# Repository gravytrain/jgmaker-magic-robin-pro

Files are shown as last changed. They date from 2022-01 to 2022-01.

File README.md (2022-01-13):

# Firmware For JGMaker Magic with MKS Robin Pro Board

## Official JGMaker ArtistD Firmware 
* Get the latest release of the Official Firmware: https://github.com/JGMaker3dofficial/artistd/releases/latest
## Official JGMaker Magic Firmware 
* Get the Official Firmware: https://github.com/JGMaker3dofficial/magic
## MKS Robin Pro Pinouts
[MKS Robin Pro Pinout](https://github.com/makerbase-mks/MKS-Robin-Pro/blob/master/hardware/MKS%20Robin%20Pro%20V1.0_001/MKS%20Robin%20Pro%20V1.0_001%20PIN.pdf)

## Setting up the new board

1.  Label all the wires as you remove them from the hotend connector.
2.  Fan connections only have a negative wire.
3.  The X-Endstop Ground wire is shared with the TH1- wire. If you reverse the TH1 - and + wires you will throw a thermal error when you trigger the X-Endstop connection.  Fix by reversing the TH1 wires.
### Mounting the board

1. Included in this project is a very basic mount 'MKS_Robin_Pro_Mount.stl'.  The board is mounted offset from the original alignment because the USB and Card slots cant align with this board.  There is enough offset to connect a usb cable and be able to slide the SD Card in and out of the slot.
2. Attach the board to the mount using (4) M3x8mm Screws with M3 nuts on the back.
3. Use 3 old board screws to secure the mount to the frame. The 4th hole under the new board will remain unattached, but doesnt affect the secureness of the mount.
### Hotend Pinout
                      Connector Clip Orientation -->
                      +--------+
                 X-S  |1*     6|  TH1+ (PC1)
      TH1-/X-G (PC1)  |2      7|  J1- (12/24v)
         HE0+ (PF10)  |3      8|  PB1- (FAN)
         HE0+ (PF10)  |4      9|  HE0- (PF10)
         HE0+ (PF10)  |5     10|  HE0- (PF10)
                      +--------+
             
### Bed Pinout

1. Connect both Red Wires together into PA0-.
2. Connect both Black Wires together into PA0+.
3. Connect the two remaining White wires to TB(PC0) for Bed Thermistor ( you will need to extend the length of these two wires so that the bed can freely move back and forth without pulling these wires tight).

### UART Board Jumpers

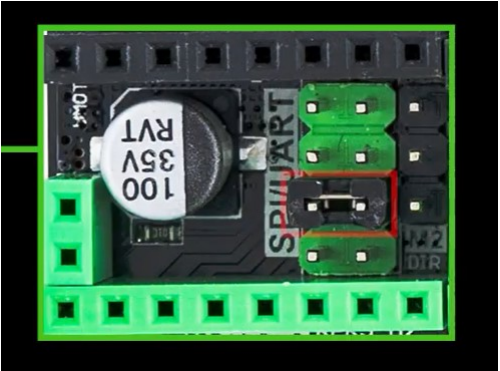
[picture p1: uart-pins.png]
Uart Board Jumpers


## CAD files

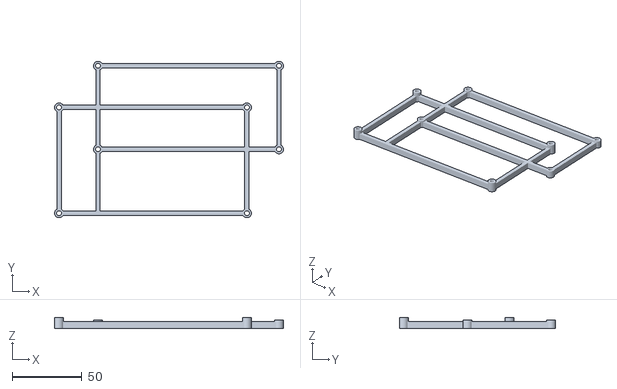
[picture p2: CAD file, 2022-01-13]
MKS_Robin_Pro_Mount.stl
164.5 x 112.4 x 8.00

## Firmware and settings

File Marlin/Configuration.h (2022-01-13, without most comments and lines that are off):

#pragma once
#define CONFIGURATION_H_VERSION 020007
#define STRING_CONFIG_H_AUTHOR "DryGravyTrain" // Who made the changes.
#define CUSTOM_VERSION_FILE Version.h // Path from the root directory (no quotes)
#define SHOW_BOOTSCREEN
#define SHOW_CUSTOM_BOOTSCREEN
#define SERIAL_PORT -1
#define SERIAL_PORT_2 3
#define BAUDRATE 115200
  #define MOTHERBOARD BOARD_MKS_ROBIN_PRO
#define CUSTOM_MACHINE_NAME "Elsie & Zeke's Maker"
#define EXTRUDERS 1
#define DEFAULT_NOMINAL_FILAMENT_DIA 1.75
#define HOTEND_OFFSET_Y { 0.0, 0.5 }  //{ 0.0, 1.00 }  // (mm) relative Y-offset for each nozzle  Y轴相对喷头的偏移量    第一台为 0.2  增加向前，减小向后  CTM关闭
#define HOTEND_OFFSET_Z { 0.0, 0.1 }  // (mm) relative Z-offset for each nozzle
#define TEMP_SENSOR_0 1
#define TEMP_SENSOR_1 0
#define TEMP_SENSOR_2 0
#define TEMP_SENSOR_3 0
#define TEMP_SENSOR_4 0
#define TEMP_SENSOR_5 0
#define TEMP_SENSOR_6 0
#define TEMP_SENSOR_7 0
#define TEMP_SENSOR_BED 1  //JGMaker
#define TEMP_SENSOR_PROBE 0
#define TEMP_SENSOR_CHAMBER 0
#define DUMMY_THERMISTOR_998_VALUE 25
#define DUMMY_THERMISTOR_999_VALUE 100
#define MAX_REDUNDANT_TEMP_SENSOR_DIFF 10
#define TEMP_RESIDENCY_TIME     10  // (seconds) Time to wait for hotend to "settle" in M109
#define TEMP_WINDOW              1  // (°C) Temperature proximity for the "temperature reached" timer
#define TEMP_HYSTERESIS          3  // (°C) Temperature proximity considered "close enough" to the target
#define TEMP_BED_RESIDENCY_TIME 10  // (seconds) Time to wait for bed to "settle" in M190
#define TEMP_BED_WINDOW          1  // (°C) Temperature proximity for the "temperature reached" timer
#define TEMP_BED_HYSTERESIS      3  // (°C) Temperature proximity considered "close enough" to the target
#define HEATER_0_MINTEMP   5
#define HEATER_1_MINTEMP   0
#define HEATER_2_MINTEMP   0
#define HEATER_3_MINTEMP   0
#define HEATER_4_MINTEMP   0
#define HEATER_5_MINTEMP   0
#define HEATER_6_MINTEMP   0
#define HEATER_7_MINTEMP   0
#define BED_MINTEMP        5
#define HEATER_0_MAXTEMP 275
#define HEATER_1_MAXTEMP 275
#define HEATER_2_MAXTEMP 275
#define HEATER_3_MAXTEMP 275
#define HEATER_4_MAXTEMP 275
#define HEATER_5_MAXTEMP 275
#define HEATER_6_MAXTEMP 275
#define HEATER_7_MAXTEMP 275
#define BED_MAXTEMP      130 //TwinkieXLII
#define PIDTEMP
#define BANG_MAX 255     // Limits current to nozzle while in bang-bang mode; 255=full current
#define PID_MAX BANG_MAX // Limits current to nozzle while PID is active (see PID_FUNCTIONAL_RANGE below); 255=full current
#define PID_K1 0.95      // Smoothing factor within any PID loop
  #define PID_AUTOTUNE_MENU     // Add PID auto-tuning to the "Advanced Settings" menu. (~250 bytes of PROGMEM)
    #define DEFAULT_Kp  22.20
    #define DEFAULT_Ki   1.08
    #define DEFAULT_Kd 114.00
#define MAX_BED_POWER 255 // limits duty cycle to bed; 255=full current
  #define PID_FUNCTIONAL_RANGE 10 // If the temperature difference between the target temperature and the actual temperature
#define PREVENT_COLD_EXTRUSION
#define EXTRUDE_MINTEMP 170
#define PREVENT_LENGTHY_EXTRUDE
#define EXTRUDE_MAXLENGTH 2000
#define THERMAL_PROTECTION_HOTENDS // Enable thermal protection for all extruders
#define THERMAL_PROTECTION_BED     // Enable thermal protection for the heated bed
#define USE_XMIN_PLUG
#define USE_YMIN_PLUG
#define USE_ZMIN_PLUG
#define ENDSTOPPULLUPS
#define X_MIN_ENDSTOP_INVERTING true  // Set to true to invert the logic of the endstop.
#define Y_MIN_ENDSTOP_INVERTING true  // Set to true to invert the logic of the endstop.
#define Z_MIN_ENDSTOP_INVERTING true  // Set to true to invert the logic of the endstop.
#define X_MAX_ENDSTOP_INVERTING true  // Set to true to invert the logic of the endstop.
#define Y_MAX_ENDSTOP_INVERTING true  // Set to true to invert the logic of the endstop.  //TwinkieXLII  已确认正确
#define Z_MAX_ENDSTOP_INVERTING true // Set to true to invert the logic of the endstop. //DryGravyTrain
#define Z_MIN_PROBE_ENDSTOP_INVERTING true // Set to true to invert the logic of the probe. //DryGravyTrain
#define X_DRIVER_TYPE TMC2209
#define Y_DRIVER_TYPE TMC2209
#define Z_DRIVER_TYPE TMC2209
#define E0_DRIVER_TYPE TMC2209
#define DISTINCT_E_FACTORS   //TwinkieXLII
#define DEFAULT_AXIS_STEPS_PER_UNIT   { 80, 80, 800, 88 } //DryGravyTrain
#define DEFAULT_MAX_FEEDRATE          { 300, 300, 5, 25 } //DryGravyTrain
#define DEFAULT_MAX_ACCELERATION      { 2000, 2000, 100, 10000 } //{ 500, 500, 100, 10000 }  TwinkieXLII
#define DEFAULT_ACCELERATION          500    // X, Y, Z and E acceleration for printing moves
#define DEFAULT_RETRACT_ACCELERATION  500    // E acceleration for retracts
#define DEFAULT_TRAVEL_ACCELERATION   500    // X, Y, Z acceleration for travel (non printing) moves
#define DEFAULT_EJERK    5.0  // May be used by Linear Advance
  #define JUNCTION_DEVIATION_MM 0.013 // (mm) Distance from real junction edge
  #define JD_HANDLE_SMALL_SEGMENTS    // Use curvature estimation instead of just the junction angle
#define S_CURVE_ACCELERATION
#define Z_MIN_PROBE_USES_Z_MIN_ENDSTOP_PIN
#define PROBE_MANUALLY
#define MANUAL_PROBE_START_Z 0.2 //TwinkieXLII
#define NOZZLE_TO_PROBE_OFFSET { 0, 0, 0 }
#define PROBING_MARGIN 10
#define XY_PROBE_SPEED (133*60)
#define Z_PROBE_SPEED_FAST HOMING_FEEDRATE_Z
#define Z_PROBE_SPEED_SLOW (Z_PROBE_SPEED_FAST / 2)
#define Z_CLEARANCE_DEPLOY_PROBE   10 // Z Clearance for Deploy/Stow
#define Z_CLEARANCE_BETWEEN_PROBES  5 // Z Clearance between probe points
#define Z_CLEARANCE_MULTI_PROBE     5 // Z Clearance between multiple probes
#define Z_PROBE_LOW_POINT          -2 // Farthest distance below the trigger-point to go before stopping
#define Z_PROBE_OFFSET_RANGE_MIN -20
#define Z_PROBE_OFFSET_RANGE_MAX 20
#define X_ENABLE_ON 0
#define Y_ENABLE_ON 0
#define Z_ENABLE_ON 0
#define E_ENABLE_ON 0 // For all extruders
#define DISABLE_X false
#define DISABLE_Y false
#define DISABLE_Z false
#define DISABLE_E false             // Disable the extruder when not stepping
#define DISABLE_INACTIVE_EXTRUDER true  // Keep only the active extruder enabled //DryGravyTrain
#define INVERT_X_DIR true   //DryGravyTrain
#define INVERT_Y_DIR false
#define INVERT_Z_DIR false
#define INVERT_E0_DIR false   //DryGravyTrain
#define INVERT_E1_DIR false
#define INVERT_E2_DIR false
#define INVERT_E3_DIR false
#define INVERT_E4_DIR false
#define INVERT_E5_DIR false
#define INVERT_E6_DIR false
#define INVERT_E7_DIR false
#define X_HOME_DIR -1
#define Y_HOME_DIR -1
#define Z_HOME_DIR -1
#define X_BED_SIZE 230
#define Y_BED_SIZE 230
#define X_MIN_POS -13 //DryGravyTrain
#define Y_MIN_POS -13
#define Z_MIN_POS 0
#define X_MAX_POS X_BED_SIZE
#define Y_MAX_POS Y_BED_SIZE
#define Z_MAX_POS 250
#define MIN_SOFTWARE_ENDSTOPS
  #define MIN_SOFTWARE_ENDSTOP_X
  #define MIN_SOFTWARE_ENDSTOP_Y
#define MAX_SOFTWARE_ENDSTOPS
  #define MAX_SOFTWARE_ENDSTOP_X
  #define MAX_SOFTWARE_ENDSTOP_Y
  #define MAX_SOFTWARE_ENDSTOP_Z
#define FILAMENT_RUNOUT_SENSOR
  #define NUM_RUNOUT_SENSORS   1     // Number of sensors, up to one per extruder. Define a FIL_RUNOUT#_PIN for each. //DryGravyTrain
  #define FIL_RUNOUT_STATE     HIGH  // Pin state indicating that filament is NOT present.
  #define FIL_RUNOUT_PULLUP          // Use internal pullup for filament runout pins.
  #define FILAMENT_RUNOUT_SCRIPT "M600"
  #define FILAMENT_RUNOUT_DISTANCE_MM 100  //TwinkieXLII
#define MESH_BED_LEVELING
#define RESTORE_LEVELING_AFTER_G28  //TwinkitXLII
#define DEBUG_LEVELING_FEATURE
  #define ENABLE_LEVELING_FADE_HEIGHT
  #define SEGMENT_LEVELED_MOVES
  #define LEVELED_SEGMENT_LENGTH 5.0 // (mm) Length of all segments (except the last one)
  #define G26_MESH_VALIDATION
    #define MESH_TEST_NOZZLE_SIZE    0.4  // (mm) Diameter of primary nozzle.
    #define MESH_TEST_LAYER_HEIGHT   0.2  // (mm) Default layer height for the G26 Mesh Validation Tool.
    #define MESH_TEST_HOTEND_TEMP  205    // (°C) Default nozzle temperature for the G26 Mesh Validation Tool.
    #define MESH_TEST_BED_TEMP      60    // (°C) Default bed temperature for the G26 Mesh Validation Tool.
    #define G26_XY_FEEDRATE         20    // (mm/s) Feedrate for XY Moves for the G26 Mesh Validation Tool.
    #define G26_RETRACT_MULTIPLIER   1.0  // G26 Q (retraction) used by default between mesh test elements.
  #define MESH_INSET 10          // Set Mesh bounds as an inset region of the bed
  #define GRID_MAX_POINTS_X 4    // Don't use more than 7 points per axis, implementation limited.
  #define GRID_MAX_POINTS_Y GRID_MAX_POINTS_X
#define LCD_BED_LEVELING  //TwinkieXLII
  #define MESH_EDIT_Z_STEP  0.025 // (mm) Step size while manually probing Z axis.
  #define LCD_PROBE_Z_RANGE 4     // (mm) Z Range centered on Z_MIN_POS for LCD Z adjustment
  #define MESH_EDIT_MENU        // Add a menu to edit mesh points
#define LEVEL_BED_CORNERS
  #define LEVEL_CORNERS_INSET_LFRB { 40, 40, 40, 40 } // (mm) Left, Front, Right, Back insets
  #define LEVEL_CORNERS_HEIGHT      0.0   // (mm) Z height of nozzle at leveling points
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

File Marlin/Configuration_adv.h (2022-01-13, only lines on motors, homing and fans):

#define E0_AUTO_FAN_PIN -1
#define E1_AUTO_FAN_PIN -1
#define E2_AUTO_FAN_PIN -1
#define E3_AUTO_FAN_PIN -1
#define E4_AUTO_FAN_PIN -1
#define E5_AUTO_FAN_PIN -1
#define E6_AUTO_FAN_PIN -1
#define E7_AUTO_FAN_PIN -1
#define CHAMBER_AUTO_FAN_PIN -1
#define HOMING_BUMP_MM      { 5, 5, 2 }       // (mm) Backoff from endstops after first bump
#define HOMING_BUMP_DIVISOR { 2, 2, 4 }       // Re-Bump Speed Divisor (Divides the Homing Feedrate)
#define QUICK_HOME                          // If G28 contains XY do a diagonal move first
#define HOME_AFTER_DEACTIVATE  // Require rehoming after steppers are deactivated
#define BACKLASH_COMPENSATION   //  TwinkieXLII
  #define BACKLASH_DISTANCE_MM { 0, 0, 0 } // (mm)
  #define BACKLASH_CORRECTION    1         // 0.0 = no correction; 1.0 = full correction
  #define BACKLASH_SMOOTHING_MM 3 // (mm)  TwinkieXLII
  #define BACKLASH_GCODE  //TwinkieXLII
    #define MEASURE_BACKLASH_WHEN_PROBING
      #define BACKLASH_MEASUREMENT_LIMIT       0.5   // (mm)
      #define BACKLASH_MEASUREMENT_RESOLUTION  0.005 // (mm)
      #define BACKLASH_MEASUREMENT_FEEDRATE    Z_PROBE_SPEED_SLOW // (mm/min)
#define MICROSTEP_MODES { 16, 16, 16, 16, 16, 16 } // [1,2,4,8,16]
#define ADVANCED_OK
#define ADVANCED_PAUSE_FEATURE //TwinkieXLII
  #define ADVANCED_PAUSE_PURGE_FEEDRATE        3  // (mm/s) Extrude feedrate (after loading). Should be slower than load feedrate.
  #define ADVANCED_PAUSE_PURGE_LENGTH         50  // (mm) Length to extrude after loading.
  #define ADVANCED_PAUSE_RESUME_PRIME          1  // (mm) Extra distance to prime nozzle after returning from park.
  #define ADVANCED_PAUSE_FANS_PAUSE               // Turn off print-cooling fans while the machine is paused.
    #define X_CURRENT       800        // (mA) RMS current. Multiply by 1.414 for peak current.
    #define X_CURRENT_HOME  X_CURRENT  // (mA) RMS current for sensorless homing
    #define X_MICROSTEPS     16    // 0..256
    #define Y_CURRENT       800
    #define Y_CURRENT_HOME  Y_CURRENT
    #define Y_MICROSTEPS     16
    #define Z_CURRENT       800
    #define Z_CURRENT_HOME  Z_CURRENT
    #define Z_MICROSTEPS     16
    #define E0_CURRENT      800
    #define E0_MICROSTEPS    16
  #define X_HYBRID_THRESHOLD     100  // [mm/s]
  #define X2_HYBRID_THRESHOLD    100
  #define Y_HYBRID_THRESHOLD     100
  #define Y2_HYBRID_THRESHOLD    100
  #define Z_HYBRID_THRESHOLD       3
  #define Z2_HYBRID_THRESHOLD      3
  #define Z3_HYBRID_THRESHOLD      3
  #define Z4_HYBRID_THRESHOLD      3
  #define E0_HYBRID_THRESHOLD     30
  #define E1_HYBRID_THRESHOLD     30
  #define E2_HYBRID_THRESHOLD     30
  #define E3_HYBRID_THRESHOLD     30
  #define E4_HYBRID_THRESHOLD     30
  #define E5_HYBRID_THRESHOLD     30
  #define E6_HYBRID_THRESHOLD     30
  #define E7_HYBRID_THRESHOLD     30

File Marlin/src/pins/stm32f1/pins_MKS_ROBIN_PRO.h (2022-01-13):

/**
 * Marlin 3D Printer Firmware
 * Copyright (c) 2020 MarlinFirmware [https://github.com/MarlinFirmware/Marlin]
 *
 * Based on Sprinter and grbl.
 * Copyright (c) 2011 Camiel Gubbels / Erik van der Zalm
 *
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
 */
#pragma once

/**
 * MKS Robin pro (STM32F103ZET6) board pin assignments
 */

#if NOT_TARGET(__STM32F1__)
  #error "Oops! Select an STM32F1 board in 'Tools > Board.'"
#elif HOTENDS > 3 || E_STEPPERS > 3
  #error "MKS Robin pro supports up to 3 hotends / E-steppers. Comment out this line to continue."
#endif

#define BOARD_INFO_NAME "MKS Robin pro"

//
// Release PB4 (Y_ENABLE_PIN) from JTAG NRST role
//
#define DISABLE_DEBUG

//#define  SDCARD_EEPROM_EMULATION

#define SPI_EEPROM
#define SPI_CHAN_EEPROM1                        2
#define SPI_EEPROM1_CS                          PB12 
#define MARLIN_EEPROM_SIZE 						0x1000   // 4KB
#define E2END 									0xFFF

// Note: MKS Robin board is using SPI2 interface.
//
#define SPI_MODULE                           2
#define ENABLE_SPI2

//
// Servos
//
#define SERVO0_PIN                          PA8   // BLTOUCH

//
// Limit Switches
//
#define X_MIN_PIN                           PA15
#define X_MAX_PIN                           PG7
#define Y_MIN_PIN                           PA12
#define Y_MAX_PIN                           PG8
#define Z_MIN_PIN                           PA11
#define Z_MAX_PIN                           PC4

//
// Steppers
//
#define X_ENABLE_PIN                        PE4
#define X_STEP_PIN                          PE3
#define X_DIR_PIN                           PE2
#ifndef X_CS_PIN
  #define X_CS_PIN                          PF8
#endif

#define Y_ENABLE_PIN                        PE1
#define Y_STEP_PIN                          PE0
#define Y_DIR_PIN                           PB9
#ifndef Y_CS_PIN
  #define Y_CS_PIN                          PF3
#endif

#define Z_ENABLE_PIN                        PB8
#define Z_STEP_PIN                          PB5
#define Z_DIR_PIN                           PB4
#ifndef Z_CS_PIN
  #define Z_CS_PIN                          PF6
#endif

#define E0_ENABLE_PIN                       PB3
#define E0_STEP_PIN                         PD6
#define E0_DIR_PIN                          PD3
#ifndef E0_CS_PIN
  #define E0_CS_PIN                         PG15
#endif

#define E1_ENABLE_PIN                       PA3
#define E1_STEP_PIN                         PA6
#define E1_DIR_PIN                          PA1
#ifndef E1_CS_PIN
  #define E1_CS_PIN                         PG10
#endif

#define E2_ENABLE_PIN                       PF0
#define E2_STEP_PIN                         PF2
#define E2_DIR_PIN                          PF1
#ifndef E2_CS_PIN
  #define E2_CS_PIN                         PG9
#endif

//SPI FLASH
#define SPI_FLASH
#define HAS_SPI_FLASH                          1
#if ENABLED(SPI_FLASH)
	#define 	W25QXX_CS_PIN		  	PB12
	#define 	W25QXX_MOSI_PIN			PB15
	#define 	W25QXX_MISO_PIN			PB14
	#define 	W25QXX_SCK_PIN			PB13
#endif

//
// Software SPI pins for TMC2130 stepper drivers
//
#if ENABLED(TMC_USE_SW_SPI)
  #ifndef TMC_SW_MOSI
    #define TMC_SW_MOSI                     PB15
  #endif
  #ifndef TMC_SW_MISO
    #define TMC_SW_MISO                     PB14
  #endif
  #ifndef TMC_SW_SCK
    #define TMC_SW_SCK                      PB13
  #endif
#endif

#if HAS_TMC_UART
  /**
   * TMC2208/TMC2209 stepper drivers
   *
   * Hardware serial communication ports.
   * If undefined software serial is used according to the pins below
   */
  //#define X_HARDWARE_SERIAL  MSerial1
  //#define Y_HARDWARE_SERIAL  MSerial1
  //#define Z_HARDWARE_SERIAL  MSerial1
  //#define E0_HARDWARE_SERIAL MSerial1
  //#define E1_HARDWARE_SERIAL MSerial1
  //#define E2_HARDWARE_SERIAL MSerial1

  //
  // Software serial
  //
  #define X_SERIAL_TX_PIN                   PF7
  #define X_SERIAL_RX_PIN                   PF8

  #define Y_SERIAL_TX_PIN                   PF4
  #define Y_SERIAL_RX_PIN                   PF3

  #define Z_SERIAL_TX_PIN                   PF5
  #define Z_SERIAL_RX_PIN                   PF6

  #define E0_SERIAL_TX_PIN                  PG13
  #define E0_SERIAL_RX_PIN                  PG15

  #define E1_SERIAL_TX_PIN                  PG12
  #define E1_SERIAL_RX_PIN                  PG10

  #define E2_SERIAL_TX_PIN                  PC13
  #define E2_SERIAL_RX_PIN                  PG9
  #define TMC_BAUD_RATE 19200
#endif

//
// Temperature Sensors
//
#define TEMP_0_PIN                          PC1   // TH1
#define TEMP_1_PIN                          PC2   // TH2
#define TEMP_2_PIN                          PC3   // TH3
#define TEMP_BED_PIN                        PC0   // TB1

//
// Heaters / Fans
//
#define HEATER_0_PIN                        PF10  // +HE0-
#define HEATER_1_PIN                        PB0   // +HE1-
#define HEATER_2_PIN                        PF9   // +HE2-
#define HEATER_BED_PIN                      PA0   // +HOT-BED-
#define FAN_PIN                             PB1   // +FAN-
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

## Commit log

2022-01-13 added updated configurations and mount stl files
    [Configuration.h, Configuration_adv.h, MKS_Robin_Pro_Mount.stl]
2022-01-13 clearly labelling TH1/X-G wiring
2022-01-13 uart pinout

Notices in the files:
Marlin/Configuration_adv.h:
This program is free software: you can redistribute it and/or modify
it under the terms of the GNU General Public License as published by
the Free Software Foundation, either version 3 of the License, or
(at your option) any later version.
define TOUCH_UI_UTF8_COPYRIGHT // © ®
